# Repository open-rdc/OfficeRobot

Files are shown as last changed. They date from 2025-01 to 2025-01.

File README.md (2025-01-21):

# OfficeRobot

設計したオフィスロボットのCADデータを共有します。

Autodesk Inventor 2023

## ロボットアーム




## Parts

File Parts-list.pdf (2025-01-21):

## 合計金額(2025/01/12時点)

¥221,095

購入先 | 型番 | URL | 単価(税抜き） | 必要数 | 購入金額(税込み)
MISUMI | CBE3-8 | https://jp.misumi-ec.com/vona2/detail/110302280360/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 ¥58 | | 18 | ¥1,148
MISUMI | CBE3-5 | https://jp.misumi-ec.com/vona2/detail/110302280360/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 ¥70 | | 8 | ¥616
MISUMI | HFBCM3-8 | https://jp.misumi-ec.com/vona2/detail/110300463610/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 ¥72 | | 16 | ¥1,267
MISUMI | CBSTSR2.5-6 | https://jp.misumi-ec.com/vona2/detail/110302280540/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 ¥260 | | 9 | ¥2,574
MISUMI | SCB5-25 | https://jp.misumi-ec.com/vona2/detail/110300239250/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 ¥252 | | 4 | ¥1,109
MISUMI | SCB5-10 | https://jp.misumi-ec.com/vona2/detail/110300239250/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 ¥226 | | 6 | ¥1,492
MISUMI | SCB5-8 | https://jp.misumi-ec.com/vona2/detail/110300239250/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 ¥237 | | 2 | ¥521
MISUMI | HNTU5-5 | https://jp.misumi-ec.com/vona2/detail/110302608140/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 ¥52 | | 12 | ¥686
MISUMI | FWSJJ-D5-V2.6-T2.5 | https://jp.misumi-ec.com/vona2/detail/110300235320/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 ¥260 | | 9 | ¥2,574
MISUMI | FB-305530 | https://jp.misumi-ec.com/vona2/detail/221000748329/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 ¥29 | | 4 | ¥128
MISUMI | FB-2001 | https://jp.misumi-ec.com/vona2/detail/221000748329/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 ¥30 | | 6 | ¥198
MISUMI | NFS5-2020-215-AV15-BV180 | https://jp.misumi-ec.com/vona2/detail/110311092599/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 ¥545 | | 1 | ¥600
MISUMI | NFS5-2020-170-AV15-BV145 | https://jp.misumi-ec.com/vona2/detail/110311092599/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 ¥545 | | 1 | ¥600
MISUMI | CSH-316L-M2-6 | https://jp.misumi-ec.com/vona2/detail/223303781021/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 ¥152 | | 4 | ¥669
MISUMI | CSH-316LM2.5-6 | https://jp.misumi-ec.com/vona2/detail/223303781021/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 ¥129 | | 6 | ¥851
MISUMI | CSH-316LM2.5-8 | https://jp.misumi-ec.com/vona2/detail/223303781021/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 ¥129 | | 9 | ¥1,277
MISUMI | SSE2B6-145 | https://jp.misumi-ec.com/vona2/detail/110302586530/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 ¥7,610 | | 1 | ¥8,371
AliExpress | GIM8108-8 | https://ja.aliexpress.com/item/1005007045730032.html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 ¥18,515 | | 3 | ¥61,100
AliExpress | GIM3505-8 | https://ja.aliexpress.com/item/1005006647908292.html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 ¥19,642 | | 4 | ¥86,425
Meviy | MVSHM-AN03054-41L-KXY42 | | ¥11,787 | 1 | ¥11,787
Meviy | MVSHM-AN04050-41D-2N2EY | | ¥6,204 | 2 | ¥12,408
Meviy | MVSHM-AN04054-41D-5MELN | | ¥11,153 | 1 | ¥11,153
Meviy | MVSHM-AN02050-41C-YNWWC | | ¥3,647 | 1 | ¥3,647
Meviy | MVSHM-AN02050-41C-JKCBT | | ¥3,113 | 2 | ¥6,226
Meviy | MVSHM-AN01552-41R-U1G17 | | ¥3,669 | 1 | ¥3,669

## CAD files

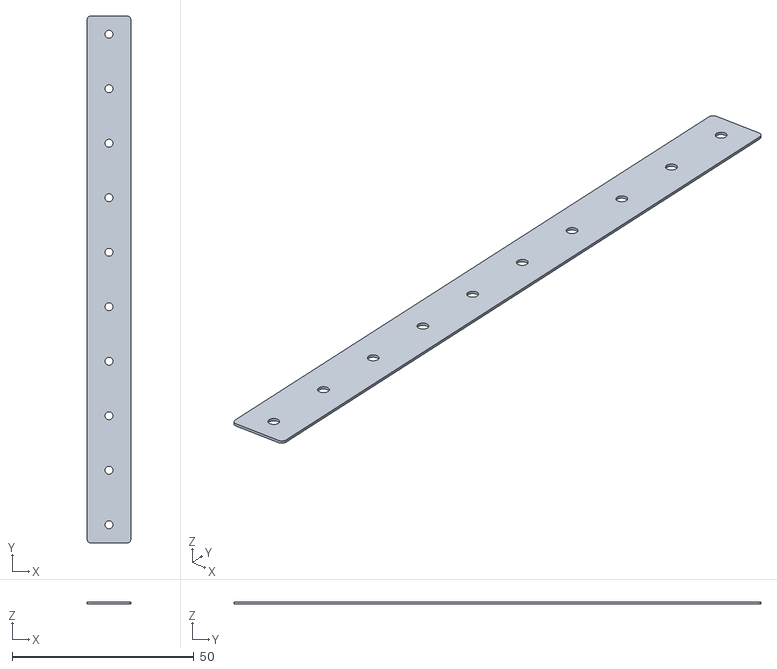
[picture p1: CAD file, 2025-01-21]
STLfile/sheet.stl
12.0 x 145.0 x 0.5

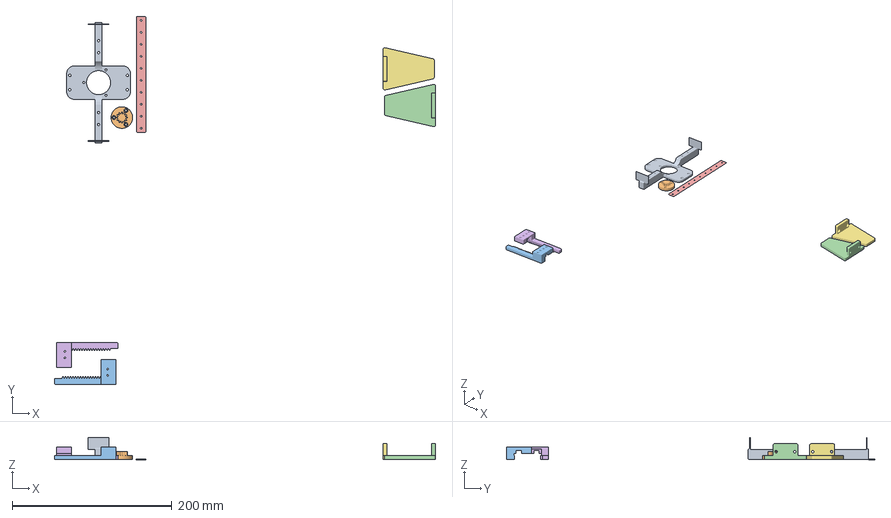
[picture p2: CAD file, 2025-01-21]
STLfile/K1Max_OrcaSlicer.3mf
476.6 x 460.6 x 28.0 mm
fix-guide-motor.stl
hand-gear.stl
linear-gear.stl x 2
nail.stl x 2
sheet.stl

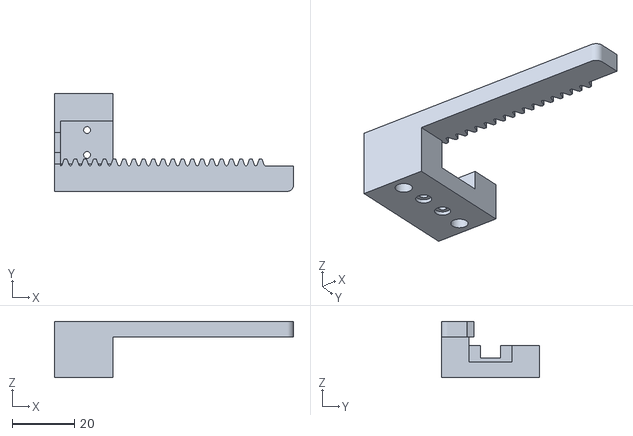
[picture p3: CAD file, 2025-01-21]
STLfile/linear-gear.stl
77.0 x 31.5 x 18.1

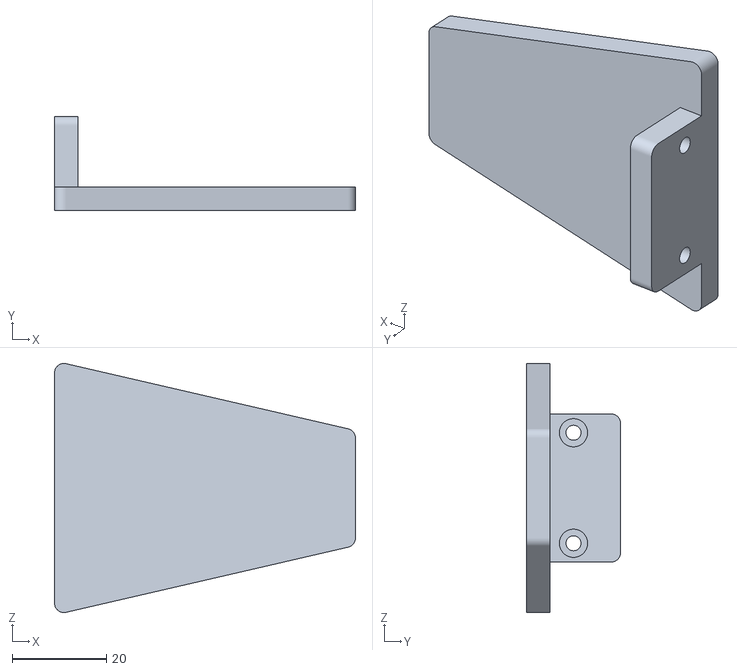
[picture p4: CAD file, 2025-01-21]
STLfile/nail.stl
64.0 x 20.0 x 53.0

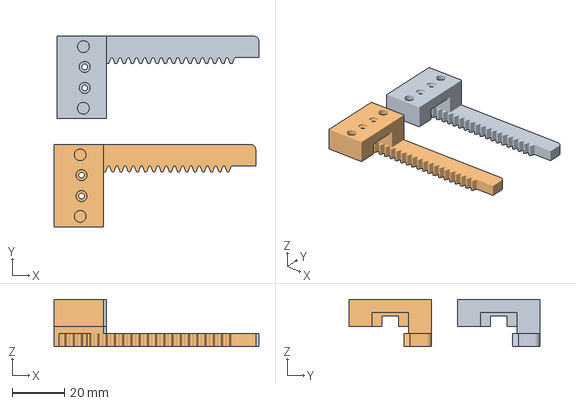
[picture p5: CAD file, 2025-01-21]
STLfile/hand-gear.3mf
78.2 x 72.8 x 18.1 mm
linear-gear.stl x 2

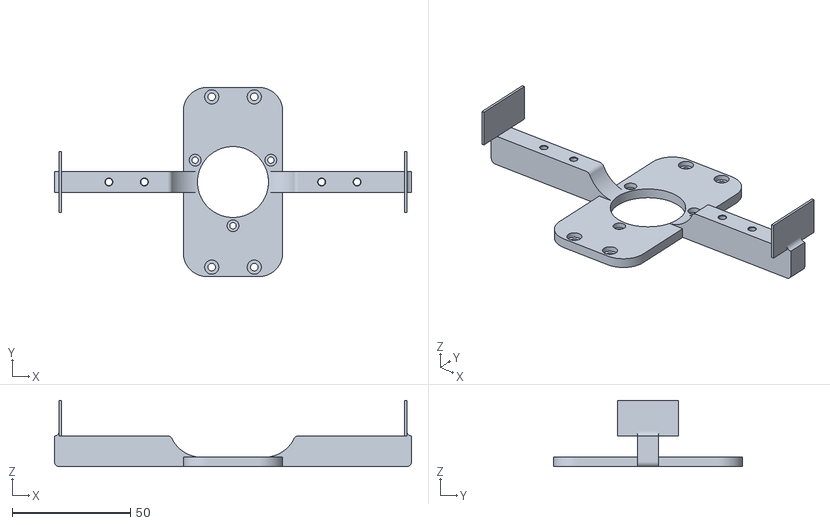
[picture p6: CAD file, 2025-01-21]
STLfile/fix-guide-motor.stl
151.0 x 80.0 x 28.0

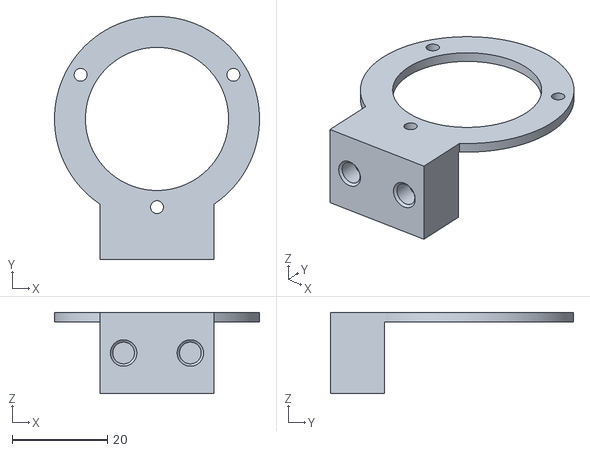
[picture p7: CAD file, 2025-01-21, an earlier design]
STLfile/OldVersion/motor-fixing.stl
43.0 x 51.0 x 17.0

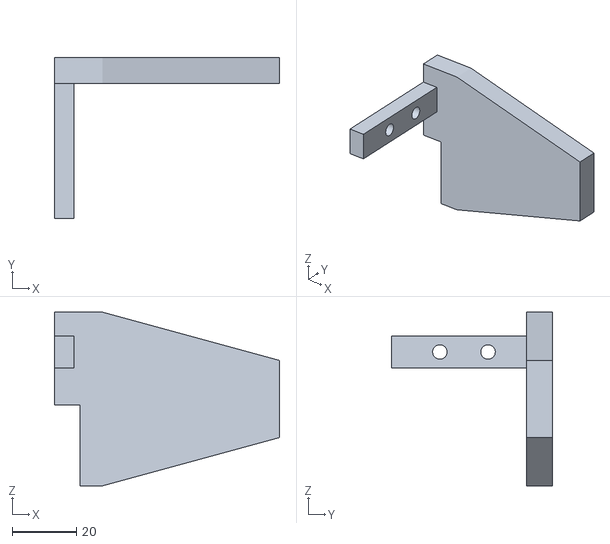
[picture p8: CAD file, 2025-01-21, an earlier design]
STLfile/OldVersion/left-nail.stl
70.0 x 50.0 x 54.0

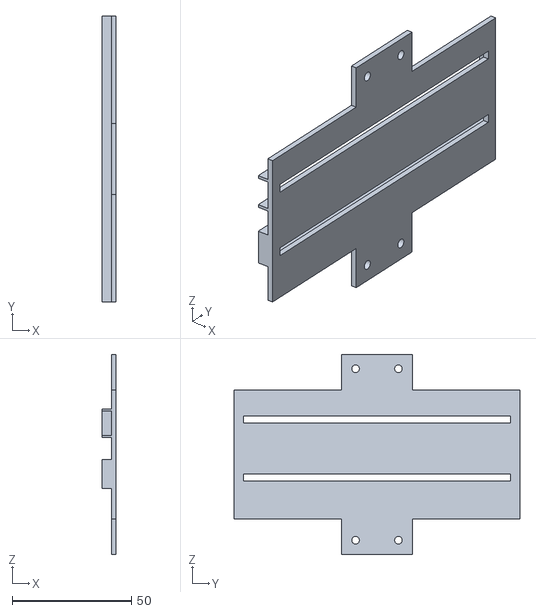
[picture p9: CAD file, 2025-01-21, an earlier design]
STLfile/OldVersion/hand_box1.stl
6.00 x 120.0 x 84.0

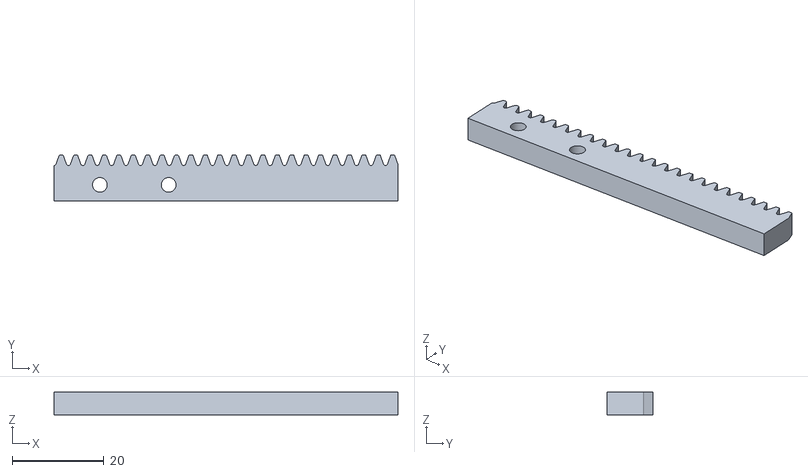
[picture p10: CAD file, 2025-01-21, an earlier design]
STLfile/OldVersion/rackgear.stl
75.0 x 10.0 x 5.00

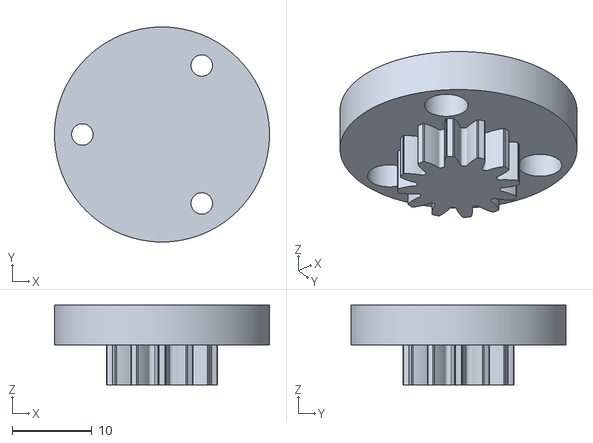
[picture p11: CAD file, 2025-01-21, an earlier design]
STLfile/OldVersion/hand-gear.stl
27.0 x 27.0 x 10.0

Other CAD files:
STLfile/OldVersion/right-nail.stl
Hand/1217OldVersion.iam
Hand/1217OldVersion/Old-linear-gear.ipt
Hand/1217OldVersion/Old-sheet.ipt
Hand/Hand.iam
Hand/Old_hand_box2.ipt
Hand/fix-guide-motor.ipt
Hand/hand-gear.ipt
Hand/hand_box1.ipt
Hand/hand_box2.ipt
Hand/left-nail.ipt
Hand/linear-gear.ipt
Hand/linear-guide-Hand.iam
Hand/motor-fixing.ipt
Hand/nail.ipt
Hand/presentation.iam
Hand/presentation.ipn
Hand/rackgear.ipt
Hand/right-nail.ipt
Hand/sheet.ipt
Manipulator/Hand.iam
Manipulator/Hand_tyokudou.iam
Manipulator/Hand_tyokudou/デザイン アクセラレータ/平歯車15.ipt
Manipulator/Hand_tyokudou/デザイン アクセラレータ/平歯車5.iam
Manipulator/Manipulator.iam
Manipulator/Manipulator.idw
Manipulator/elbow-pitch-bracket.ipt
Manipulator/elbow-pitch-plate.ipt
Manipulator/elbow-pitch-plate_T4.ipt
Manipulator/haguruma.ipt
Manipulator/hand-box.ipt
Manipulator/hand-gear.ipt
Manipulator/hand-gearbox.ipt
Manipulator/hand-nail-1.ipt
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

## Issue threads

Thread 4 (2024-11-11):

設計に関する指摘

yasuohayashibara, 2024-11-11:
以下のコミットに関する指摘
e87b89b2a190d5c0066f613ff2dd236b433d4895

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

yasuohayashibara, 2024-11-11:
１）位置合わせのピンに隙間がある．これでは役割を果たせない．
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

yasuohayashibara, 2024-11-11:
２）鋭角の部分がある．応力集中が発生するので避けた方が良い．
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

yasuohayashibara, 2024-11-11:
３）応力が加わらないところが抜かれていない．
軽量化に寄与しない，もしくは加工の費用が大きく変わる場合はこのままでも良いかもしれないが，一般的には軽量化できるところは軽量化したほうが良いと思います．

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

yasuohayashibara, 2024-11-11:
５）板金の端に穴を開けているが，加工できないと回答されることがある．
６）フィレットが無いので危険である．

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

yasuohayashibara, 2024-11-11:
７）部品同士が干渉している．

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

yasuohayashibara, 2024-11-11:
GIM3505-8はモータドライバをつけると以下のような形状になる．
モータドライバ無しの場合は設計のような接続もできるが，ネジの有効長が3mmなのと，自分でモータドライバを用意しなければならないことを考えるとハードルが高くなるかもしれない．

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

https://steadywin.cn/en/pd.jsp?id=130#_jcp=3_3

yasuohayashibara, 2024-11-11:
９）手首のピッチ方向の可動域が小さい
手首を上げて使用することが多いと思いますので，問題になると思います．

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

yasuohayashibara, 2024-11-11:
１０）ロールの回転軸が中心からズレている．
ただし，意図的にずらしているとしたら問題ない．（意図があれば伝えて下さい．）
あと，ハンドのモータがロールの軸とは一致していないので，姿勢を維持するためにロールのモータは常にトルクを出し続けなければならない．軸を一致させたほうがモータの負担が減る．

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

yasuohayashibara, 2024-11-11:
１１）ハンド部分の3Dプリンタでの出力
以下の部品はおそらくこちらの向きで出力することが必要になると思いますが，強度が不足するおそれがあるかと思います．
積層方向に部品は壊れ（剥がれ）ますので，形状を工夫したほうが良いかもしれません．

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

yasuohayashibara, 2024-11-11:
１２）この部分に力が集中しますので，壊れるおそれが高いと思います．
なお，噛み合う部分だけ歯があれば良いと思います．

手先も剥離方向に力がかかるので，強度が足りないかもしれません．
ベアリングなどの配置も記載したほうが良いと思います．

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

yasuohayashibara, 2024-11-11:
１３）安全性の議論がありませんが，どうしましょうか．
最低限の安全対策は入れることが必要だと思います．

yasuohayashibara, 2024-11-11:
４）に関して有限要素解析を簡単に行ってみた．
以下は手先に2kgを加えたときの様子であるが，たわみもそれなりに発生するので振動的になるかもしれない．
手先3kg程度が限界なので，もう少し強度（剛性）を上げたほうが良さそう．

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

Keita1Mori, 2024-11-13:
## コメント

- 貫通している理由
  - ①貫通よりかは両方からの締結がいいのではと思います
  - ②逆側からネジとアルミフレーム用後入ればねナットを用いての締結もできるのではと思います

①
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

②
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

 - 伸縮機能をできるようにした設計であれば以下の写真の部分が干渉するので注意したほうがいいと思います
 - 設計した部品とアルミフレームが干渉しています

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

- 矢印方向に応力があった場合干渉する気がします
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

MasatoKubotera, 2024-11-14:
Review Commit: 4dc32ddd848224394f6aec98a839410b3e885fca

- アルミフレームナット

後入れナット（HNTP5-5）を使用しているが，
アルミフレームの両端が常に塞がっている設計ではないので，
先入れナットの方が良いと思います．

先入れナットの方が，フレーム内でぐらつかないので，締結が楽になります．
また，ばね付きの方が締めるときに楽になると思います．

後入れナット（HNTP5-5）＞　先入ればねナット（HNTU5-5）
https://jp.misumi-ec.com/vona2/detail/110302608140/?HissuCode=HNTU5-5

- 板金部品における位置合わせのピン穴

板金部品において，通し穴の公差を指定すると担当者見積もりになりますので，
発注にひと手間加わることになりますのでご注意ください．

通し穴（公差指定なし）して隙間を詰めるとものによっては入らなくなる恐れがあります．

- pitch_plate_40mm

y軸方向に追加してネジ締結した方が良いと思います．

曲げ内側半径がR1に対して，アルミフレームの外側フィレットもR1のため，
完全に密着しない恐れがあります．
（板金の曲げ半径Rはあくまでも参考値のため）

https://jp.meviy.misumi-ec.com/help/ja/technical_info/shm_conditions/3445/

- 板金＆アルミフレームの締結精度

X軸方向に対して，板金とアルミフレーム接続位置が保障されていない．
フレームとアルミフレームの端をあわせて締結するのは難しいと思います．

elbow-pitch-bracketとアルミフレームの位置決めは特に難しいと思います．

- 通し穴の等級

曲げ加工部の寸法許容差は

基準寸法の区分6を超え30以下，板厚6.0mm以下の場合，
±0.5となりますので，M5通し穴（φ5.5・等級2）では締結できないことがありえる．

https://jp.meviy.misumi-ec.com/help/ja/technical_info/shm_conditions/3459/

- ネジ頭とフレームの隙間

隙間 0.5mmはかなり狭い気がします．最低でも1.0mmは確保した方が良いと思います．
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

- アルミフレームの端面

フレームの端面はかなり鋭利ですので，高速で駆動するものに使用するときには，注意を払った方が良いです．

yasuohayashibara, 2024-12-12:
だいぶ設計が洗練されてきたと思います．

問題ないとは思いますが，ここが長いのはあまりうれしくありません．
他のところで皿ネジを使用してるようにできればこちらも皿ネジにして，距離を縮めたほうが良いです．

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

赤：固定方法が不明です．
青：ピニオンの位置が遠ざかるほど，てこのように大きな力が加わることになります．
　　固定するネジの距離はできるだけ遠いほうが良いです．
　　まあおそらく大丈夫な気がしますが，接触する面積も含めて力学的にはあまりうれしくない設計になっています．

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

KiyoshiroKawanabe, 2024-12-13:
> 他のところで皿ネジを使用してるようにできればこちらも皿ネジにして，距離を縮めたほうが良いです．

Meviyの皿穴加工がM3からなので皿ねじの使用が難しいです．そのため，超低頭ボルトを使用して距離を縮めます．
4.5㎜ > 2.5mm

ハンドはリニアガイドを使用した設計に変更予定です．
以下のハンドを参考に設計します．
https://github.com/PCrnjak/SSG-48-adaptive-electric-gripper

KiyoshiroKawanabe, 2024-12-14:
以下のリニアガイドを使用したハンドを設計しました．
https://jp.misumi-ec.com/vona2/detail/110300042210/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

KiyoshiroKawanabe, 2025-01-21:
設計が終わり製作まで行ったのでissueを閉じます．ご指摘いただきありがとうございました．

Closed 2025-01-21.

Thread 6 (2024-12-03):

アームの基本性能と部品の安全率

KiyoshiroKawanabe, 2024-12-03:
# 軸間距離
調査したオフィスロボットのうち、アームリーチがわかったものは9台。それらの平均値は719.7mm、中央値は700㎜であった。そのためアームリーチを710㎜に調整した。
肩ピッチと肘ピッチを繋ぐリンク1と肘ピッチと手首ピッチ繋ぐリンク2の長さは、人間の腕の割合を参考に調整した。https://www.airc.aist.go.jp/dhrt/91-92/data/list.html
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
# 可搬重量
肩ピッチ軸を基準とする重心までの距離　0.315m
重量　1.53kg
自重を支えるために必要なトルク　4.72Nm
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
手先で支えられる重量
連続　0.51kg
瞬時　3.20kg
# 可動域
曲げたとき
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
伸ばしたとき
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
机と空き缶を比較のために配置。机の縁から500㎜の位置に空缶を配置。
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
# アーム手先の移動の様子
基準の位置(250,0)
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

手を伸ばした様子(450,0)
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

右遠くに伸ばした様子(450,200)
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

左遠くに伸ばした様子
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

右近くに伸ばした様子(50,200)
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

左近くに伸ばした様子(50,-200)
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

# 部品の安全率
手先で1kgの物体を把持した場合を想定し、Z軸方向への荷重で解析。
それぞれの安全率に現状の設計で問題はなかった。
- sholder_roll_bracket
手先までの距離　0.6m　
重量　1.57＋１　
荷重　15.1Nm
安全率　2.91
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
- pitch_plate_20mm(肩ピッチとアルムフレームを接続してるパーツ)
手先までの距離　0.6m　
重量　1.17+1　
荷重　12.7Nm
安全率　4.89
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
- elbow-pitch-bracket
手先までの距離　0.34　
重量　1.05+1　
荷重　6.8Nm
安全率　8.89
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
pitch_plate_20mm(肘とアルミフレームを繋ぐ部品)
手先までの距離　0.3　
重量　0.65+1　
荷重　4.8Nm
安全率　12.9
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

KiyoshiroKawanabe, 2025-01-21:
基本的な性能を示したのでissue閉じます．

Closed 2025-01-21.

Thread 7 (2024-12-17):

リニアガイドの選定

KiyoshiroKawanabe, 2024-12-17:
現在使用を検討しているミニチュアリニアガイド：[SSE2BSLZ8-140](https://jp.misumi-ec.com/vona2/detail/110300042210/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)
参考出荷日が12/24(12/17現在)
下記のものは参考出荷日が1日早く年内受け取りの可能性が高いため，こちらのリニアガイドの使用を検討している．
[SSE2B6-145](https://jp.misumi-ec.com/vona2/detail/110302586530/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)

## 比較
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
左が前者．右が後者．
ブロックが多少小さくなり，20gくらい軽くなる
価格は約1500円高い

KiyoshiroKawanabe, 2025-01-21:
サイズの都合がよかったので，[こちらのミニチュアリニアガイド](https://jp.misumi-ec.com/vona2/detail/110302586530/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)を使用します．

Closed 2025-01-21.

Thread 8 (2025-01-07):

オフィスロボット用のORNE-box発注リスト

Keita1Mori, 2025-01-07:
リストを作成したがいくつかのパーツが廃番になっていたのでその代替品を探す。

Keita1Mori, 2025-01-20:
## 更新（1/20時点）

- misumi
  - ワゴ:[862-504/594](https://jp.misumi-ec.com/vona2/detail/222005691265/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)
  - Murrplastik:[BTK17](https://jp.misumi-ec.com/vona2/detail/110500127810/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)
  - 日本航空電子工業株式会社:[MMS3102E-16-10S](https://jp.misumi-ec.com/vona2/detail/110400365720/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)
  - 日本航空電子工業株式会社:[CA2120-5-R](https://jp.misumi-ec.com/vona2/detail/222000484440/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)
  - [MMS3057-8A](https://jp.misumi-ec.com/vona2/detail/110400164730/?HissuCode=MMS3057-8A)

Keita1Mori, 2025-01-21:
- [MMS3057-8A](https://jp.misumi-ec.com/vona2/detail/110400164730/?HissuCode=MMS3057-8A) の代替品
  - [NMS3057-8A](https://jp.misumi-ec.com/vona2/detail/110500021840/)
- [MMS3102E-16-10S](https://jp.misumi-ec.com/vona2/detail/110400365720/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) の代替品
  - [JAE八紘株式会社](https://www.jae.com/hakko/stockcheck/?topics_keyword=N%2FMS3102A16-10S%09)に在庫があることを確認
  - またmouser, digikeyに類似するものも見つけた
  - [mouser](https://www.mouser.jp/ProductDetail/Amphenol-Industrial/MS3102E16-10S?qs=URCIWeoXFlTLapBsFFycXg%3D%3D)
  - [digikey](https://www.digikey.jp/ja/products/detail/amphenol-industrial-operations/MS3102E16-10S/2179954)

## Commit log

2024-11-11 modified file
    [Hand.iam, Manipulator.iam, elbow-pitch-bracket.ipt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]
2024-11-11 deleted file
    [D3040-7130B.ipt, hand.0001.iam]
2024-12-14 change STL Files
    [hand-gear.stl, hand-gearbox.stl, hand-nail-1.stl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]
2024-12-18 add 3MF file
    [K1Max_OrcaSlicer.3mf]
